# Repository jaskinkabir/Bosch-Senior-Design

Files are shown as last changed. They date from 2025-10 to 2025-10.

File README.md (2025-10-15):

# Intro
For my senior design project, my team was tasked with building an automated wash station for Bosch's grinder carts that are used to transport circular saw blades through the manufacturing process. My part of the project was designing and building the PLC system that controls the pressure washer, compressed air valves, and the wastewater pump. 

The project overview and final mechanical design can be seen in this poster
poster

# Initial Design
I began the design process by mapping out the Process Flow Diagram for the overall system, focusing on efficiency and robustness. My PLC system needed to control power to the pressure washer, the wastewater disposal pump, and the solenoid valves that control the flow of clean water, wastewater, and compressed air for drying.
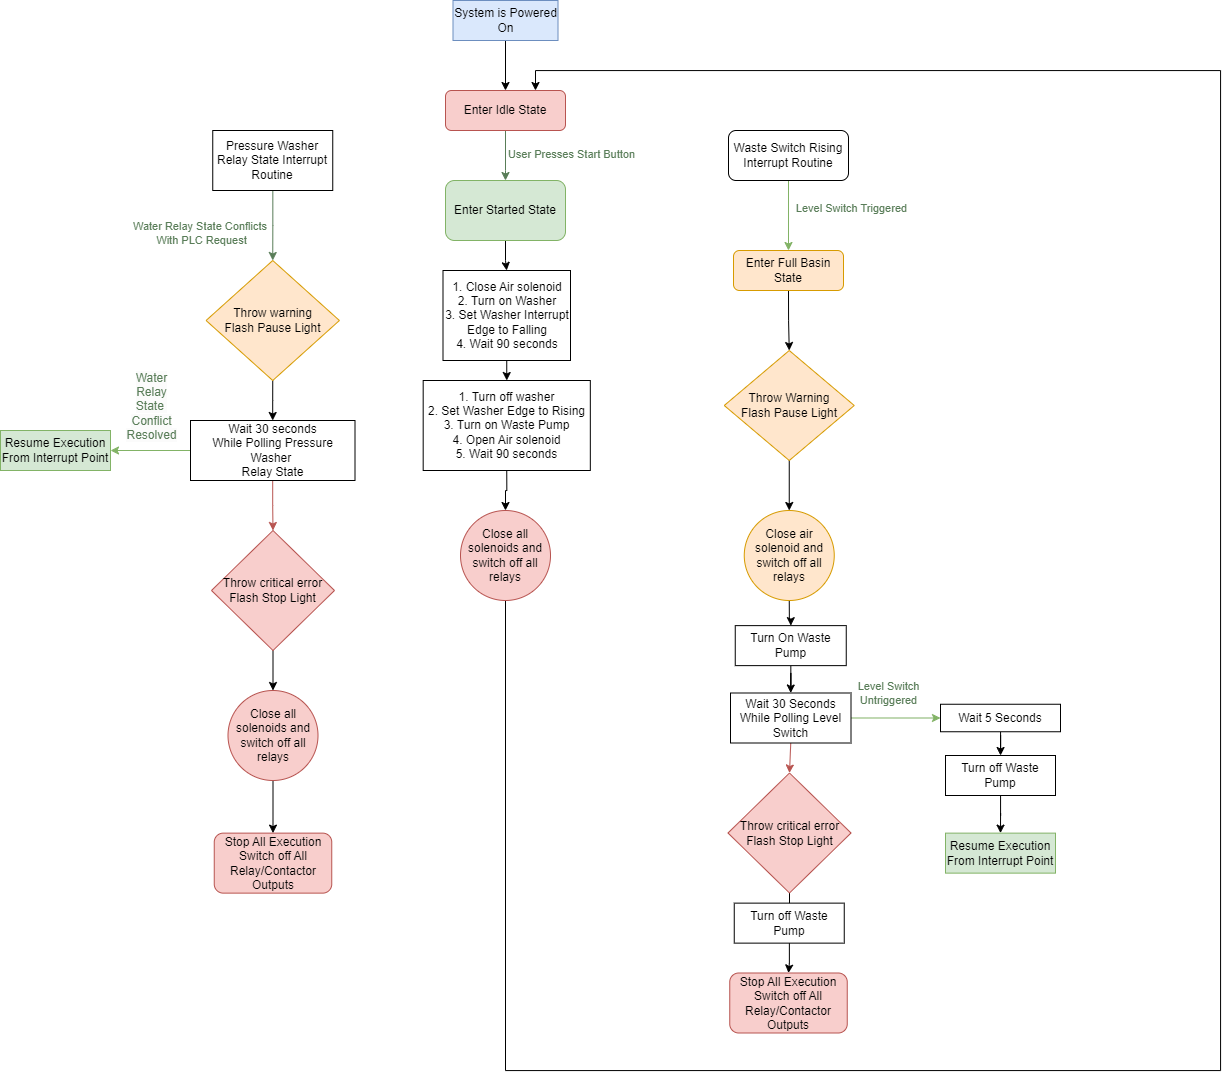
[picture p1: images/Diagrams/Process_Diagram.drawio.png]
PFD


## Relay Interlocking System
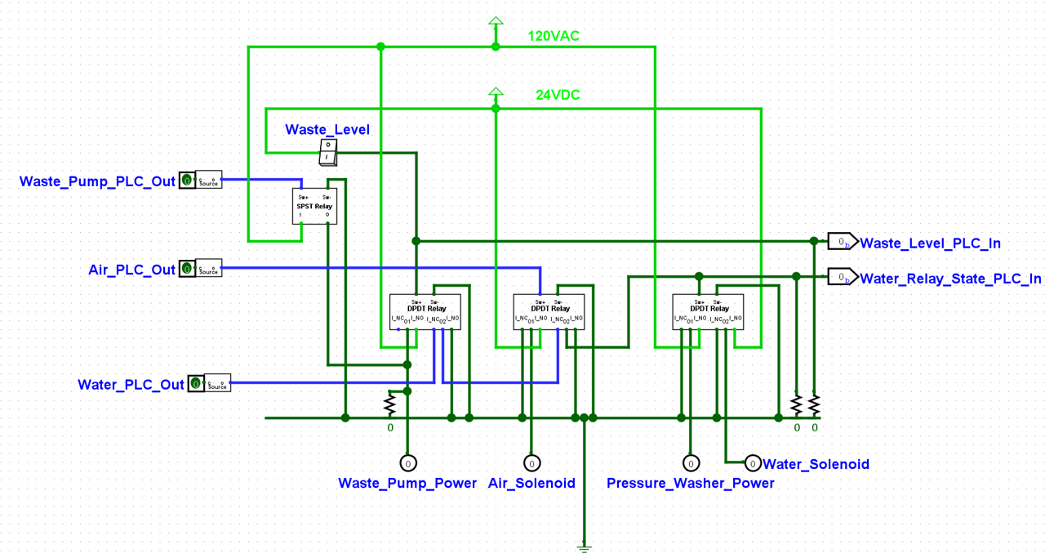
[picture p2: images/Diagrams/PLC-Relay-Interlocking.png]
relay_interlocking

I then designed a relay-interlocking system that ensures, in hardware, the following restrictions
- The pressure washer cannot be powered on, nor the water input solenoid be open while the compressed air solenoid is open
	- This is to ensure water does not enter Bosch's compressed air system
- The pressure washer cannot be powered, nor the water input solenoid be open while the wastewater level float switch is triggered. The wastewater level float switch also powers on the waste pump independently of the PLC
	- This is to ensure the system does not flood with wastewater
# PLC Design
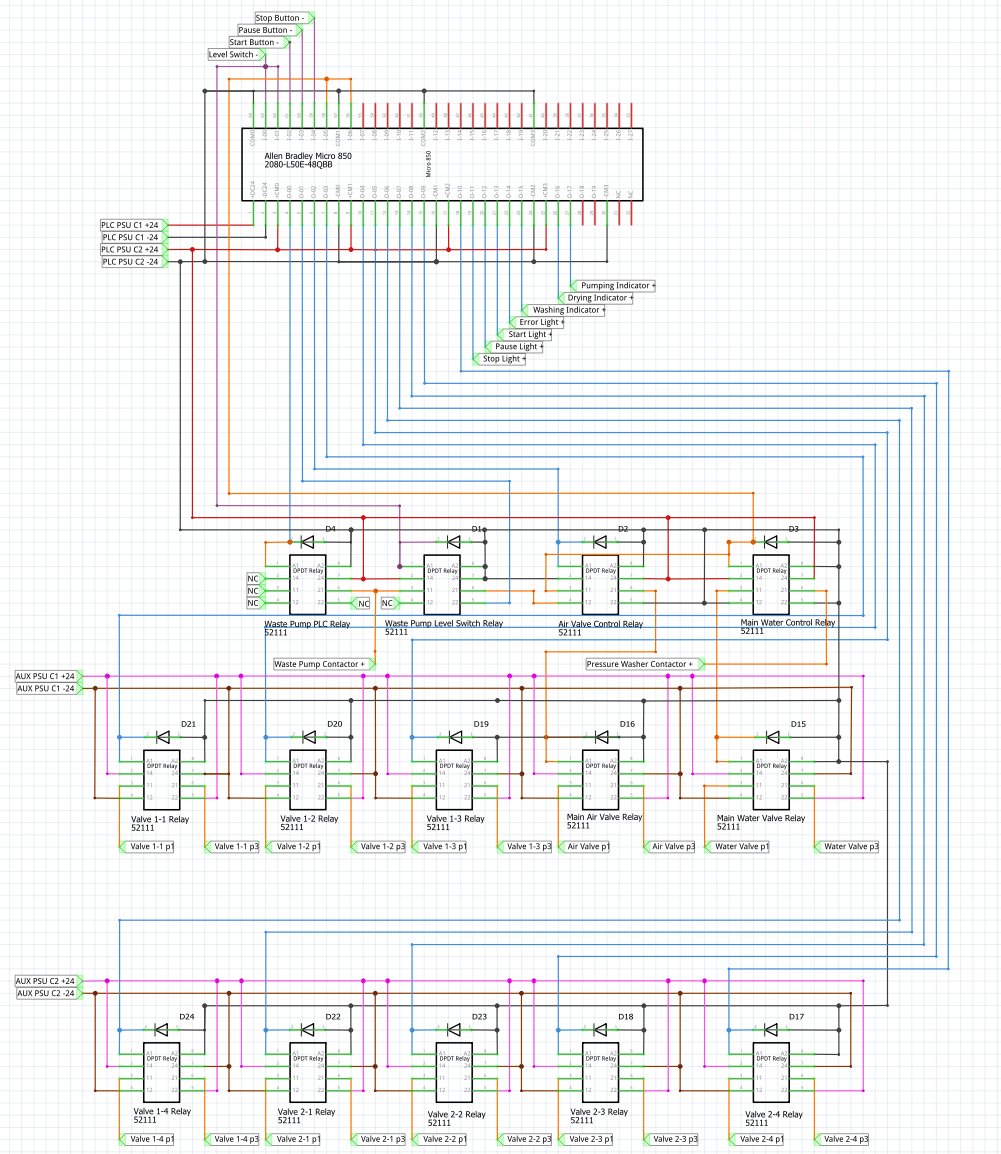
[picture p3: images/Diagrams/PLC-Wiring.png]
PLC_wiring

- Once the PLC was chosen, I created a wiring diagram for the PLC, the relays, and the relay protectors
- This diagram was extremely useful when I eventually assembled the system
## Python Netlist Analyzer
- Once I created the Fritzing diagram, I exported the netlist as an XML file
- I then wrote a Python script to analyze this netlist and convert it into a CSV file that contains each net, the number of nodes, and whether or not the net includes a node external to the PLC enclosure
- I used this CSV file for these purposes:
	- To gauge how much wire I needed to buy and of what color (since I assigned each net type a different color)
	- To figure out how many pins the external connectors needed
	- To make checking my final wiring against the initial design much easier
# Plywood Wiring
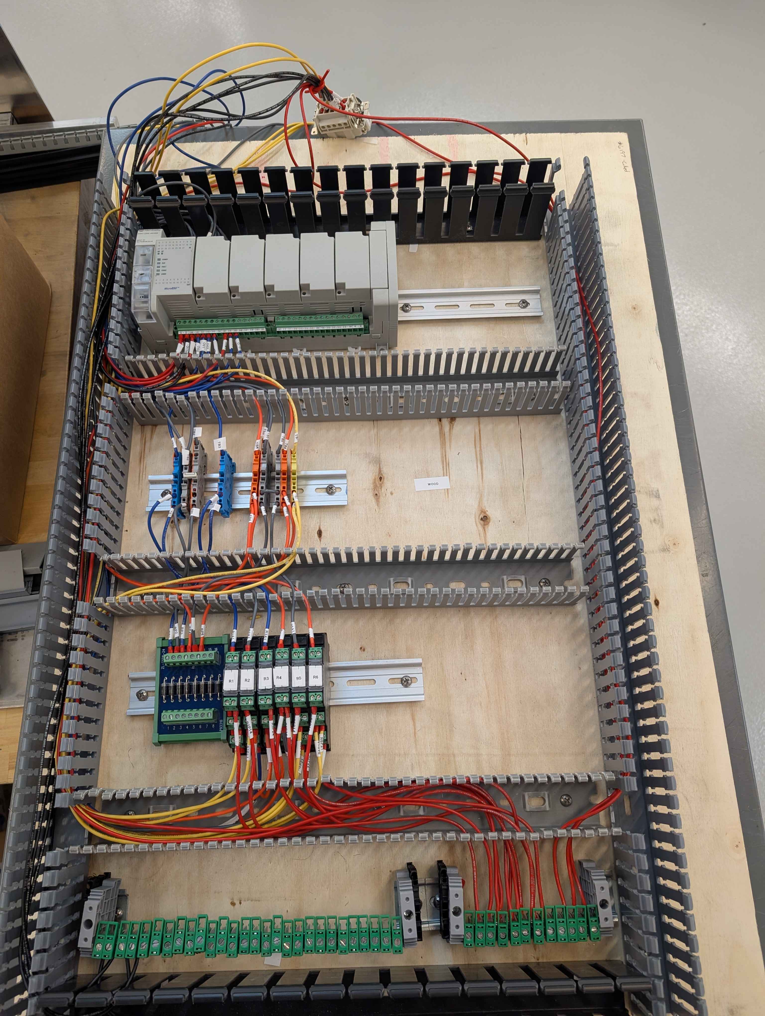
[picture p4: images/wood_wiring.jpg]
wood_wiring

- Due to ordering issues, the PLC enclosure did not arrive alongside the PLC and all its related components. 
- So as to not waste any time, I mounted all the components to a piece of plywood I bought from Home Depot and started cutting, labeling, and routing the wires according to the diagram and the CSV file
# Final Wiring
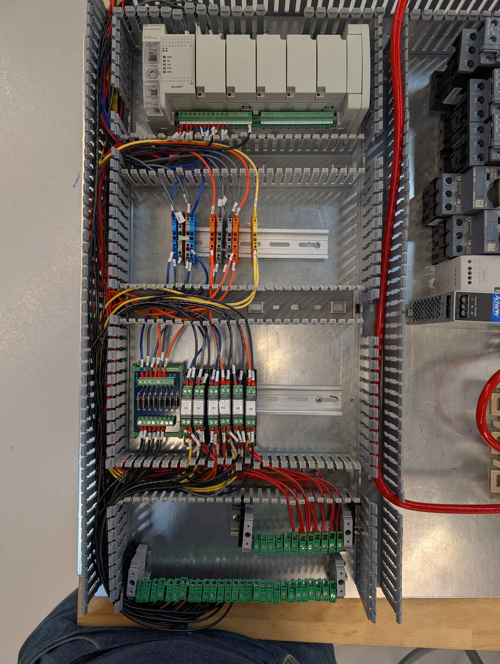
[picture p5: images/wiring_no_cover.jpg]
wiring_no_cover

final_wiring
- Once the enclosure for the PLC system arrived, I transferred over the components and wires from the plywood into the new enclosure
- I am very proud of the organization and cleanliness of the assembled system

# HMI Design
- For the control interface, I used a touchscreen HMI panel for displaying the system's state, and 3 physical buttons for controlling the machine
- I began with a wiring diagram:
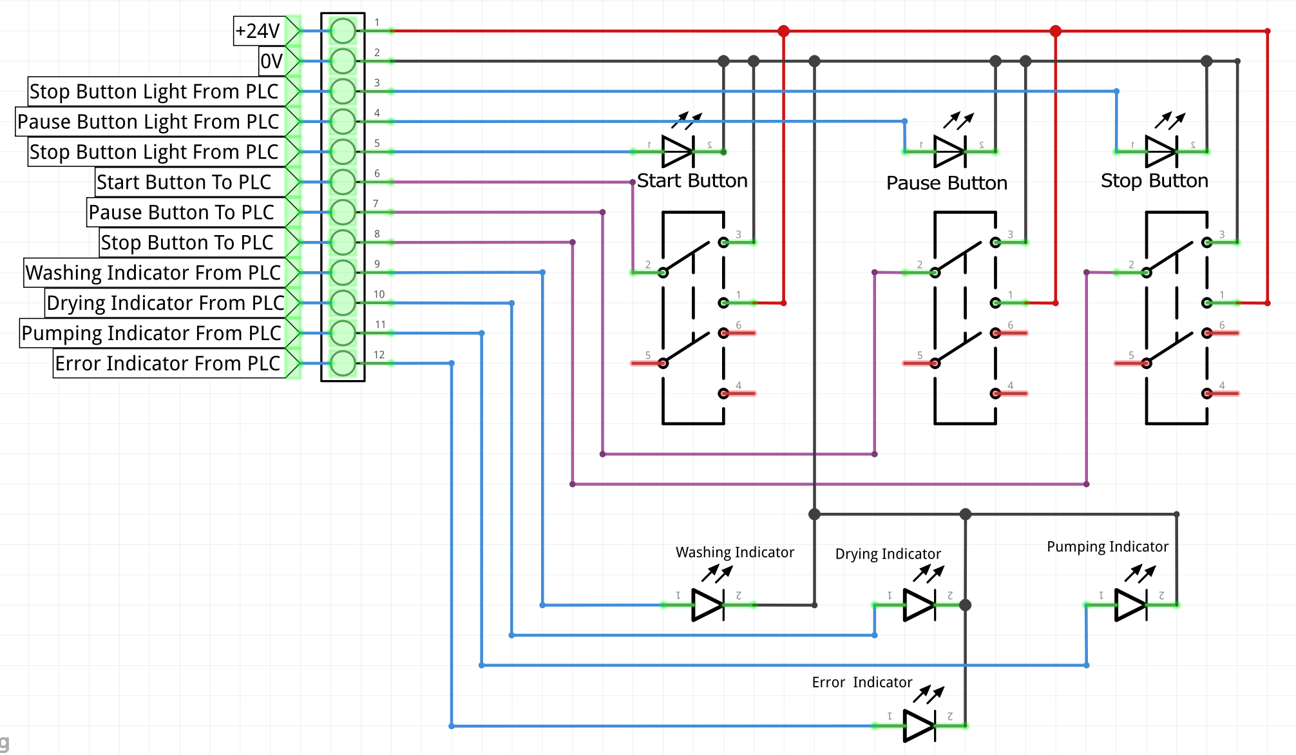
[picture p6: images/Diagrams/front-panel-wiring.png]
fp_wiring

- I then wired together the HMI enclosure and ran a waterproof cable to connect it to the PLC
# Conclusion
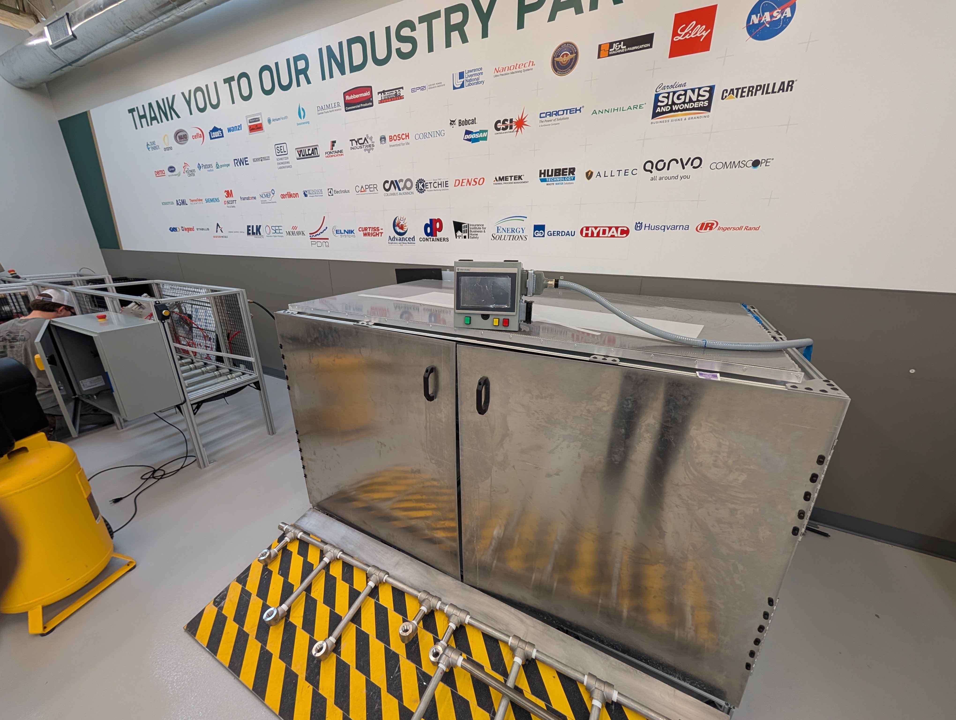
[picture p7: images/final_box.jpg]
final_box

Regrettably, due to timing constraints and ordering mishaps, I did not have the time to program the PLC. However, I still gained valuable experience from this project.

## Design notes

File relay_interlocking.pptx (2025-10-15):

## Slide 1

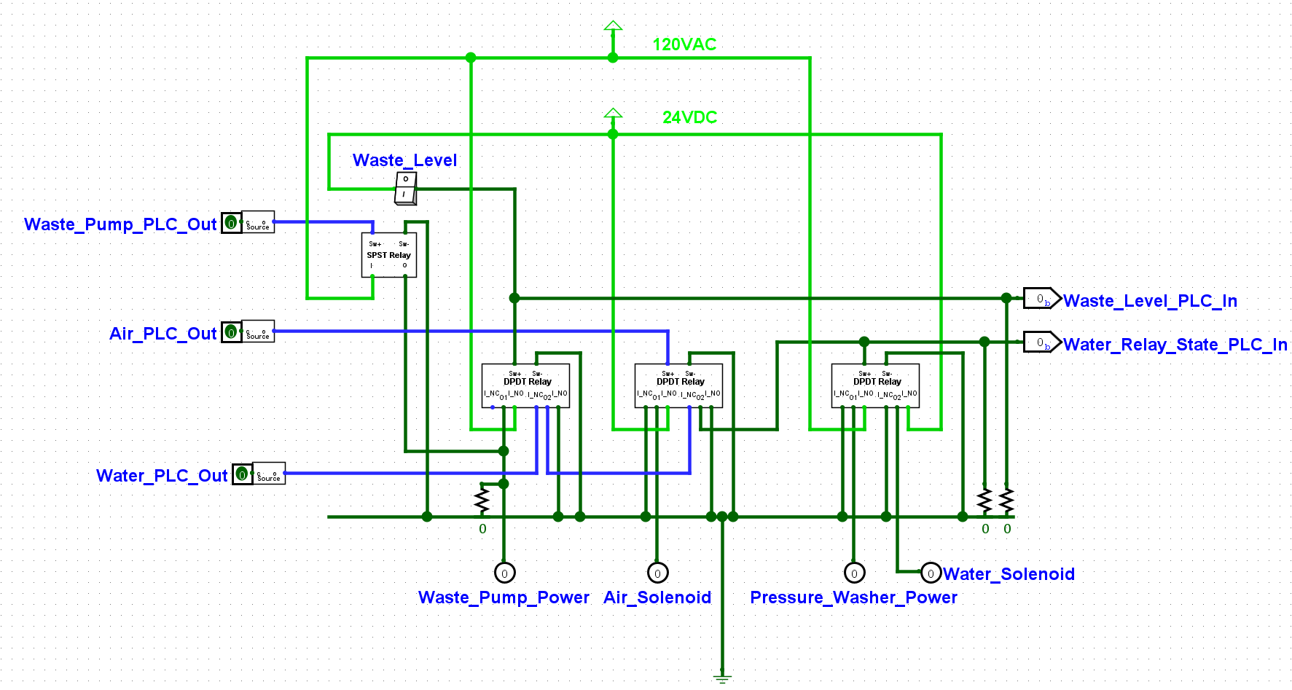
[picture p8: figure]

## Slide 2

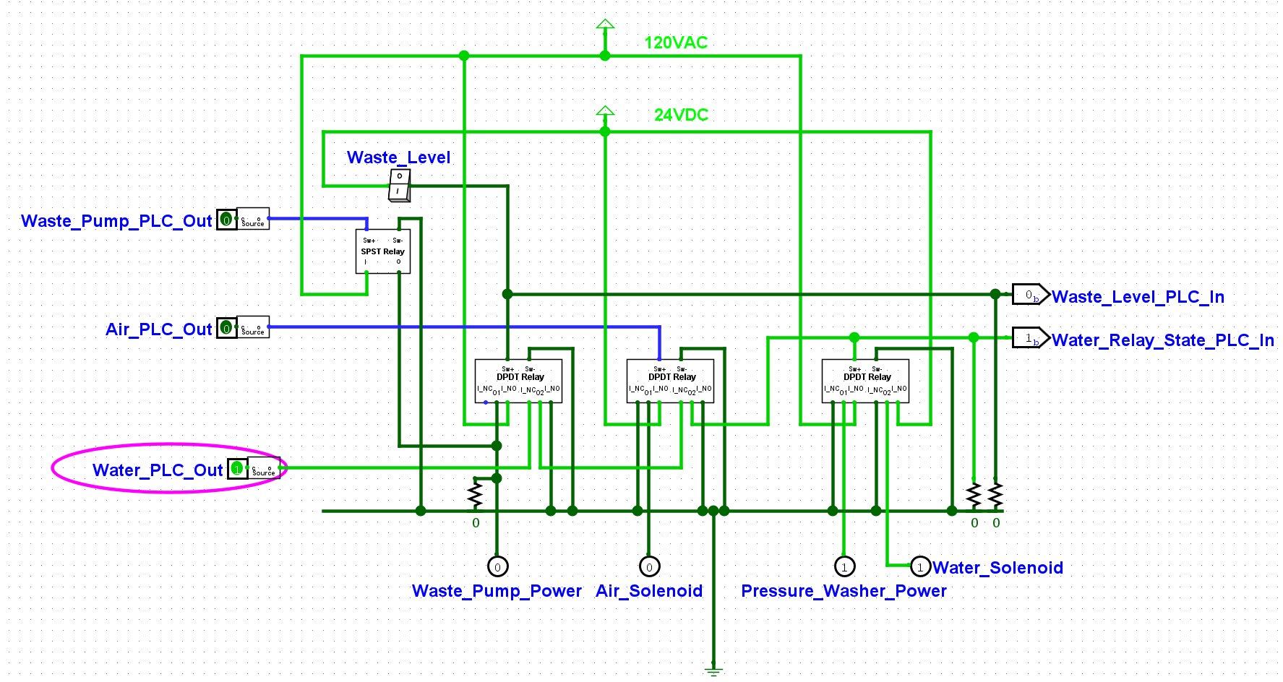
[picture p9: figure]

PLC Turns Water On

Main Water Solenoid
Receives 24VDC

Pressure washer receives 120VAC

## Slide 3

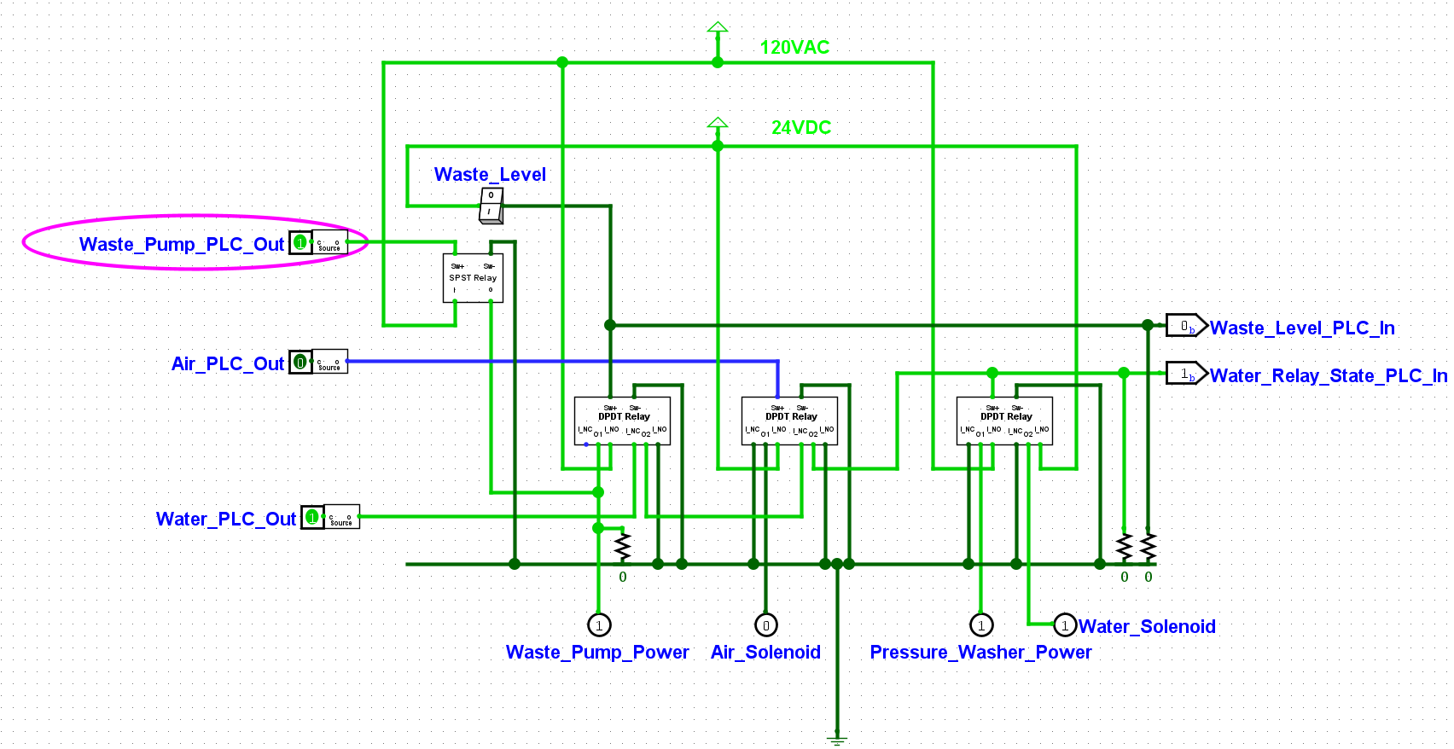
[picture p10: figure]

Waste pump enabled with short delay

Waste pump receives 120VAC

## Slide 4

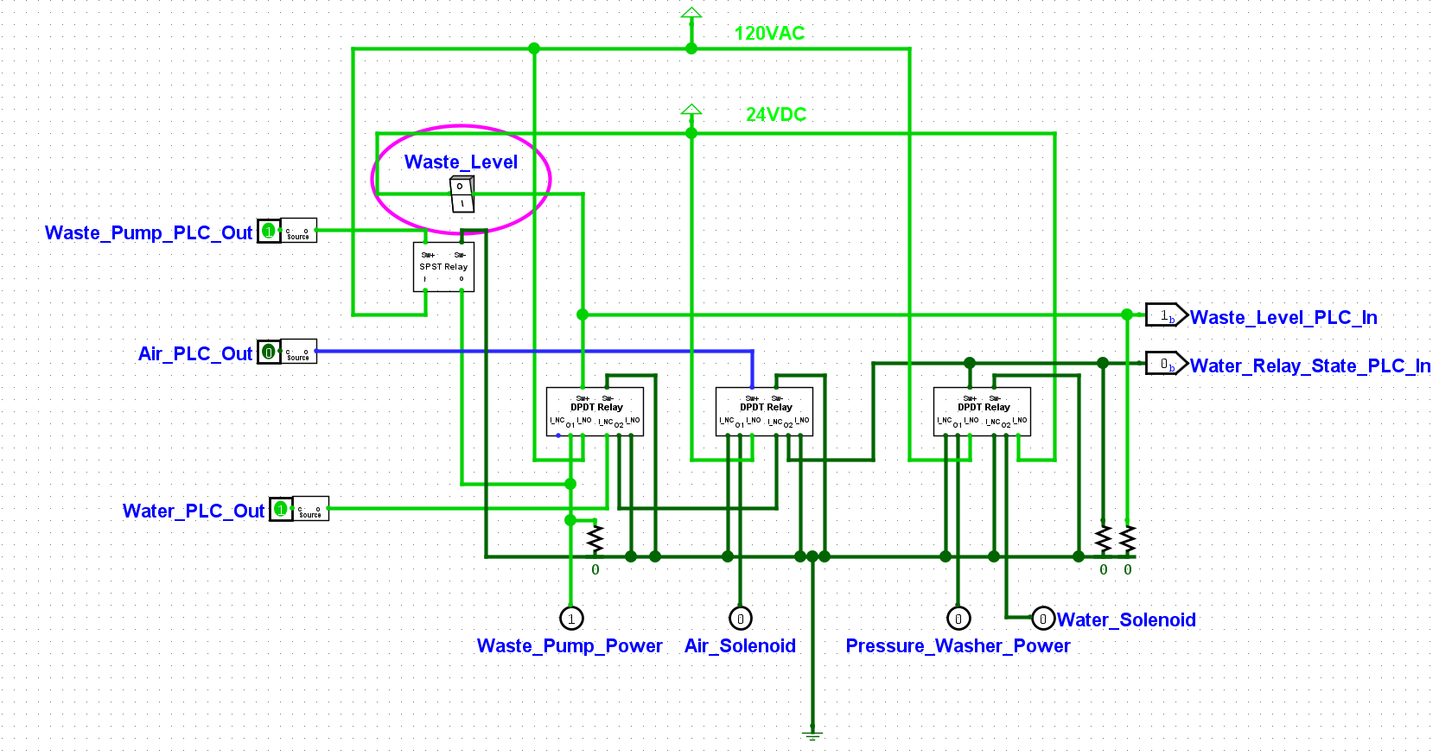
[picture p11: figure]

Waste level switch triggered

PLC can read switch state

Pressure Washer instantly turns off
and the solenoid is closed

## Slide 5

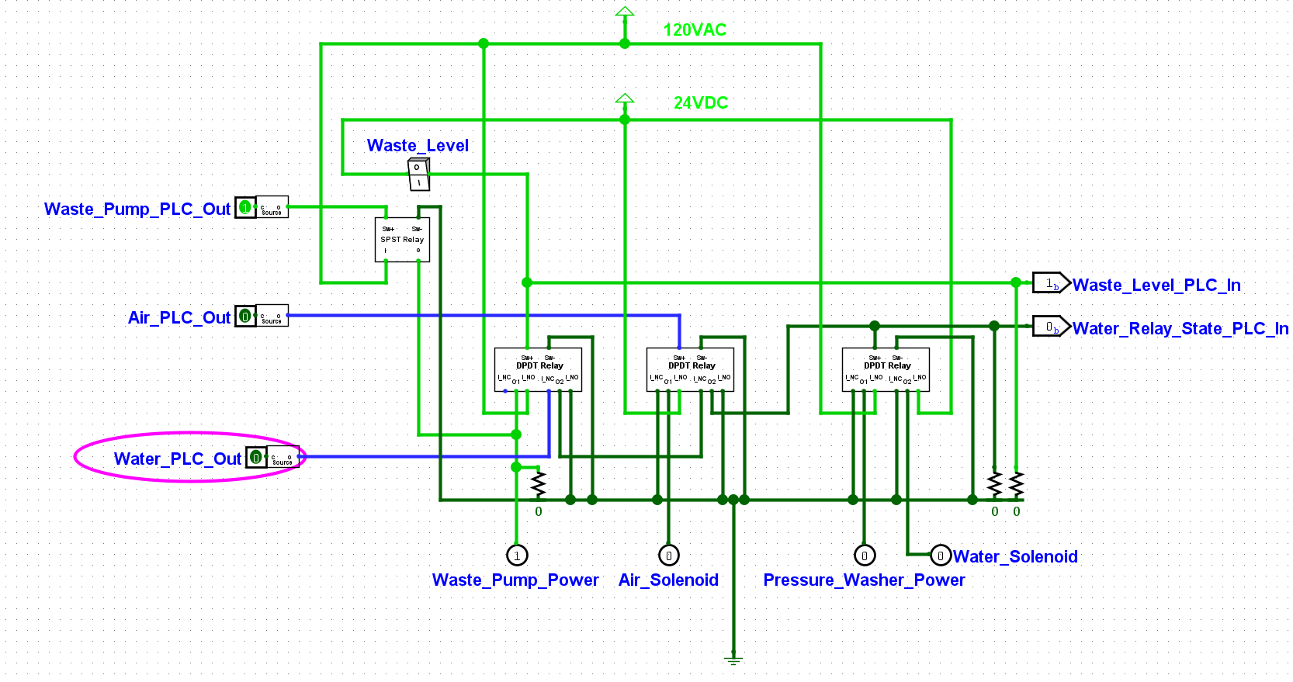
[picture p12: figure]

PLC holds pump on for set time

If level switch is still triggered after this time, throw critical error

PLC Switches its water output off
And pauses wash cycle

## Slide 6

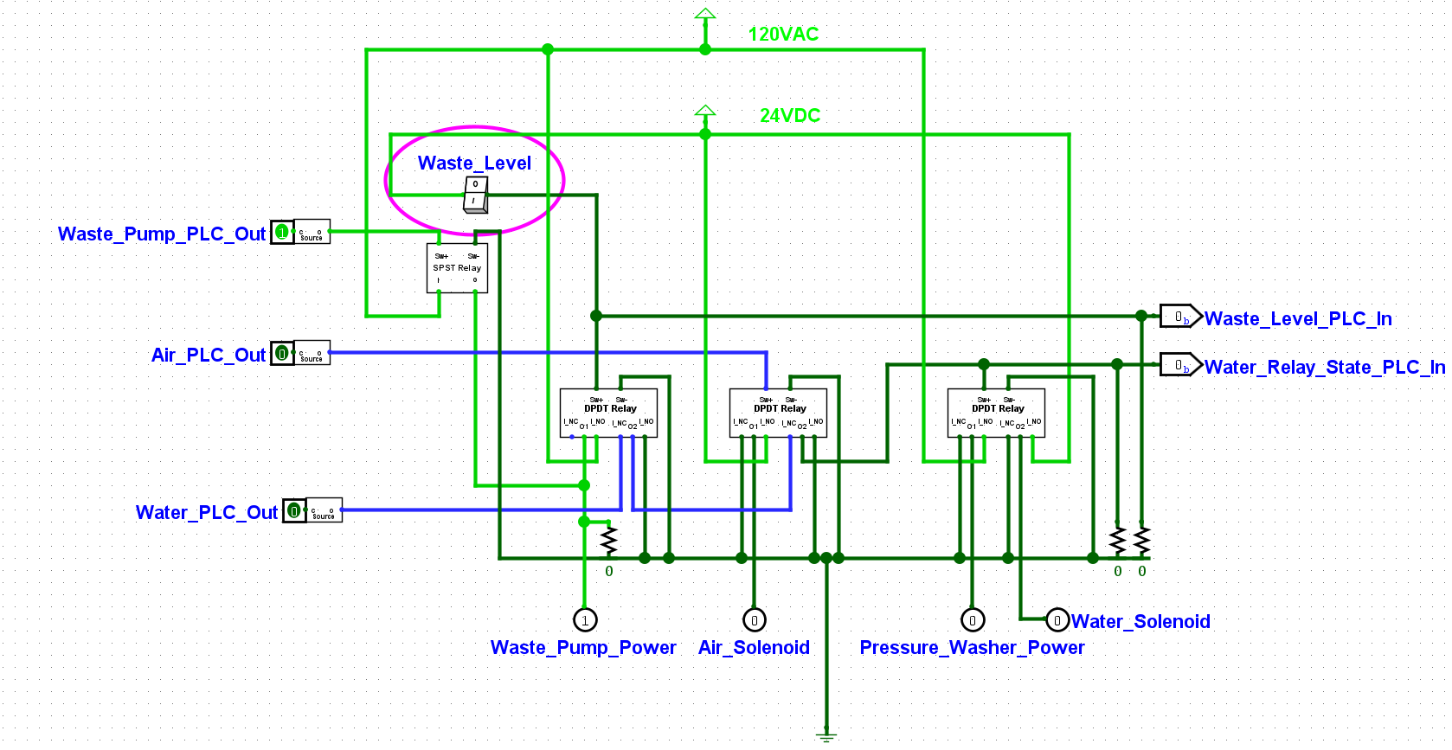
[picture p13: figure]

Level switch returns to normal position

PLC recognizes change in switch state

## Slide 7

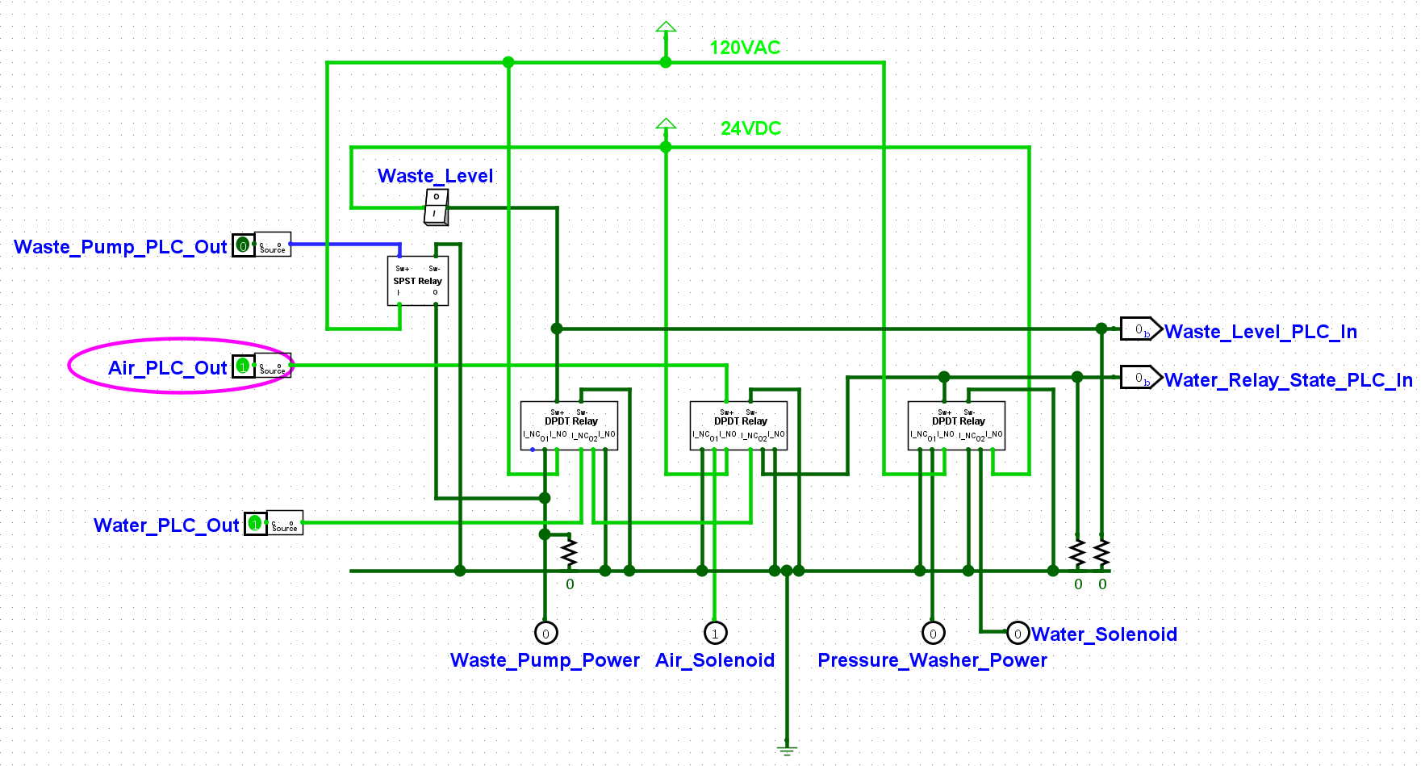
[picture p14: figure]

PLC disables waste pump in response to error

Software bug/PLC or Relay failure
opens air solenoid

PLC can recognize this error

Pressure washer turned off
Water solenoid closed

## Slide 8

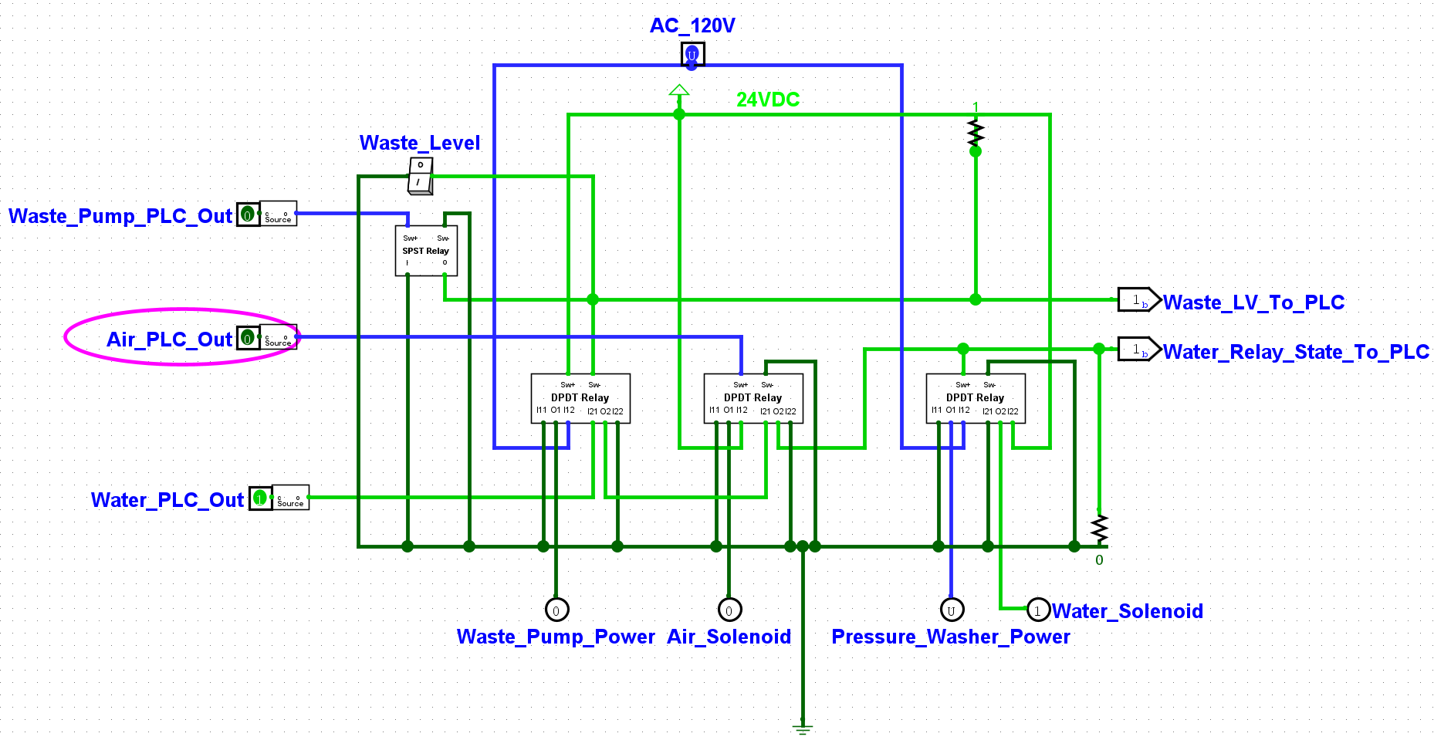
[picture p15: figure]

Bug is resolved

Resume Wash Cycle

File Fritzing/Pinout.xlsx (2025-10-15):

PIN | FUNCTION
I0 | Level Switch
I1 | Start Button
I2 | Pause Button
I3 | Stop Button
I4 | Water Solenoid State
PIN | FUNCTION
O0 | Waste Pump Relay
O1 | Pressure Washer Relay
O2 | Air Solenoid Relay
O3 | Solenoid 1-1
O4 | Solenoid 1-2
O5 | Solenoid 1-3
O6 | Solenoid 1-4
O7 | Solenoid 2-1
O8 | Solenoid 2-2
O9 | Solenoid 2-3
O10 | Solenoid 2-4
O11 | Stop Light
O12 | Pause Light
O13 | Start Light
O14 | Error Light
O15 | Washing Indicator
O16 | Drying Indicator
O17 | Pumping Indicator

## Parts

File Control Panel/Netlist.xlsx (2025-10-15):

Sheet: PLC_Diag_distributed_netlist
 | Net Name | # Nodes | External? | Type |  | Bus Rod Length | Bus bar length |  |  |  |  |  |  | 40
0 | AUX PSU C1 -24 | 64 | TRUE | AUX PSU C2 -24 | 213.3333333 | 48 | 49.9 | 19.64566929 |  |  | Net Counts |  | Wire color | Wire length | Spool length
1 | AUX PSU C2 +24 | 34 | TRUE | AUX PSU C2 +24 | 113.3333333 | 25.5 | 27.4 | 10.78740157 |  |  | AUX PSU C2 -24 | 64 | Black | 213.3333333 | 500 | 77.93 | #N/A
2 | PLC I-05 | 5 | FALSE | PLC Input |  |  |  |  |  |  | AUX PSU C2 +24 | 34 | Red | 113.3333333 | 200 | 37.4
3 | Level Switch - | 5 | TRUE | PLC Input |  |  |  |  |  |  | Logical Output | 45 | Yellow | 150 | 500 | 77.93
4 | MAV RL PA1 | 3 | FALSE | Interconnection |  |  |  |  |  |  | PLC Output | 46 | Blue | 153.3333333 | 200 | 37.4
5 | MWV RL PA1 | 3 | FALSE | Interconnection |  | 73.5 | 77.3 | Cm |  |  | PLC Input | 16 | Grey | 53.33333333 | 100 | 20.78
6 | Waste Pump Contactor + | 3 | TRUE | Logical Output |  | 28.93700787 | 30.43307087 | In |  |  | Interconnection | 8 | Orange | 26.66666667 | 25 | 6.3
7 | PLC O-00 | 3 | FALSE | PLC Output
8 | PLC O-02 | 3 | FALSE | PLC Output |  | Bus Terminals |  |  |  |  |  |  |  | 710 | 1525 | 257.74
9 | PLC O-03 | 3 | FALSE | PLC Output |  | 98 | 490 |  |  |  |  |  |  | 2.366666667 | 5.083333333
10 | PLC O-04 | 3 | FALSE | PLC Output
11 | PLC O-05 | 3 | FALSE | PLC Output |  |  | 2 port terminal blocks | 3 Port TB | 4 Port TB |  |  |  |  |  |  | 178.03
12 | PLC O-06 | 3 | FALSE | PLC Output |  | Single Circuit | 33 | 13 | 2 |  |  | 25 | 6.3
13 | PLC O-07 | 3 | FALSE | PLC Output |  | Jumped |  | 2 |  |  |  | 50 | 11.43
14 | PLC O-08 | 3 | FALSE | PLC Output |  |  |  |  |  |  |  | 100 | 20.78
15 | PLC O-09 | 3 | FALSE | PLC Output |  | Total | 33 | 15 | 2 |  |  | 200 | 37.4
16 | PLC O-10 | 3 | FALSE | PLC Output |  |  |  |  |  |  |  | 500 | 77.93
17 | MAV PLC RL P12 | 2 | FALSE | Interconnection
18 | Air Valve p1 | 2 | TRUE | Logical Output |  | 0
19 | Air Valve p3 | 2 | TRUE | Logical Output
20 | Pressure Washer Contactor + | 2 | TRUE | Logical Output |  | Meaning | Color | 2 Port | 3 port | 4 Port
21 | Valve 1-1 p1 | 2 | TRUE | Logical Output
22 | Valve 1-1 p3 | 2 | TRUE | Logical Output |  | Logical Output | Yellow | 21 | 1
23 | Valve 1-2 p1 | 2 | TRUE | Logical Output |  | PLC Output | Blue | 7 | 10
24 | Valve 1-2 p3 | 2 | TRUE | Logical Output |  | PLC Input | Grey | 3 | 2 | 2
25 | Valve 1-3 p1 | 2 | TRUE | Logical Output |  | Interconnection | Orange | 1 | 2
26 | Valve 1-3 p3 | 2 | TRUE | Logical Output
27 | Valve 1-4 p1 | 2 | TRUE | Logical Output |  | 500
28 | Valve 1-4 p3 | 2 | TRUE | Logical Output |  |  |  | 32 | 15 | 2
29 | Valve 2-1 p1 | 2 | TRUE | Logical Output
30 | Valve 2-1 p3 | 2 | TRUE | Logical Output
31 | Valve 2-2 p1 | 2 | TRUE | Logical Output
32 | Valve 2-2 p3 | 2 | TRUE | Logical Output |  | Meaning | Color | 2 Port | 3 port | 4 Port |  | Total | Length of Blocks
33 | Valve 2-3 p1 | 2 | TRUE | Logical Output
34 | Valve 2-3 p3 | 2 | TRUE | Logical Output |  | Logical Output | Yellow | 21 | 1 |  |  | 22 | 9.24
35 | Valve 2-4 p1 | 2 | TRUE | Logical Output |  | PLC Output | Blue | 8 | 10 |  |  | 18 | 7.56
36 | Valve 2-4 p3 | 2 | TRUE | Logical Output |  | Interconnection | Orange | 1 | 2 |  |  | 3 | 1.26
37 | Water Valve p1 | 2 | TRUE | Logical Output |  | PLC Input | Grey | 3 | 2 | 2 |  | 7 | 2.94
38 | Water Valve p3 | 2 | TRUE | Logical Output
39 | PLC PSU C1 +24 | 2 | TRUE | PLC PSU C1 +24 |  |  |  |  |  |  |  |  | 21
40 | PLC PSU C1 -24 | 2 | TRUE | PLC PSU C1 -24
41 | Pause Button - | 2 | TRUE | PLC Input |  |  |  | 33 | 15 | 2
42 | Start Button - | 2 | TRUE | PLC Input
43 | Stop Button - | 2 | TRUE | PLC Input
44 | PLC O-01 | 2 | FALSE | PLC Output
45 | Drying Indicator + | 2 | TRUE | PLC Output
46 | Error Light + | 2 | TRUE | PLC Output
47 | Pause Light + | 2 | TRUE | PLC Output
48 | Pumping Indicator + | 2 | TRUE | PLC Output
49 | Start Light + | 2 | TRUE | PLC Output
50 | Stop Light + | 2 | TRUE | PLC Output | 30
51 | Washing Indicator + | 2 | TRUE | PLC Output

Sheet: BOM
Part | Part # | Cost | Qty | Total Cost | Link
Bus Bar Terminal Block | 1529T11 | 1.022 | 100 | 102.2 |  | Total Cost
Bus Bar Mount | 1529T32 | 2.066 | 5 | 10.33 |  | 1061.78
Bus Bar Rod | 1529T21 | 31.42 | 1 | 31.42
Yellow 2 port Terminal Block | 9473T173 | 1.95 | 21 | 40.95 | https://www.mcmaster.com/9473T173/
Blue 2 port Terminal Block | 9473T173 | 1.95 | 8 | 15.6 | https://www.mcmaster.com/9473T173/
Orange 2 Port Terminal Block | 9473T173 | 1.95 | 1 | 1.95 | https://www.mcmaster.com/9473T173/
Grey 2 Port Terminal Block | 9473T173 | 1.95 | 3 | 5.85 | https://www.mcmaster.com/9473T173/
Yellow 3 port Terminal Block | 9473T177 | 2.58 | 1 | 2.58 | https://www.mcmaster.com/9473T177/
Blue 3 port Terminal Block | 9473T177 | 2.58 | 10 | 25.8 | https://www.mcmaster.com/9473T177/
Orange 3 Port Terminal Block | 9473T177 | 2.58 | 2 | 5.16 | https://www.mcmaster.com/9473T177/
Grey 3 Port Terminal Block | 9473T177 | 2.58 | 2 | 5.16 | https://www.mcmaster.com/9473T177/
Grey 4 Port Terminal Block | 9473T182 | 2.97 | 2 | 5.94 | https://www.mcmaster.com/9473T182/
Jumper | 9473T194 | 1.51 | 2 | 3.02 | https://www.mcmaster.com/9473T194/
16 Pin Connector Male | ZP-MC16B-1-MC016-2 | 8 | 6 | 48 | https://www.automationdirect.com/adc/shopping/catalog/wiring_solutions/multi-wire_connectors/inserts/zp-mc16b-1-mc016-2 |  |  | Worked from 3-8:55 9/4
16 Pin Connector Female | ZP-MC16B-1-FC016-2 | 7.25 | 3 | 21.75 | https://www.automationdirect.com/adc/shopping/catalog/wiring_solutions/multi-wire_connectors/inserts/zp-mc16b-1-fc016-2
16 Pin Connector Hood | ZP-MC16B-2-STE21M | 14.5 | 3 | 43.5 | https://www.automationdirect.com/adc/shopping/catalog/wiring_solutions/multi-wire_connectors/housings/zp-mc16b-2-ste21m
16 Pin Connector Base | ZP-MC16B-2-SBHC | 25 | 3 | 75 | https://www.automationdirect.com/adc/shopping/catalog/wiring_solutions/multi-wire_connectors/housings/zp-mc16b-2-sbhc
Code Pins | ZP-MC-CODEPIN-2 | 10.5 | 1 | 10.5 | https://www.automationdirect.com/adc/shopping/catalog/wiring_solutions/multi-wire_connectors/code_pins_-z-_polarization_keys/zp-mc-codepin-2
Crimp Contacts Male | ZP-MC-CC-M16A-18 | 34.5 | 1 | 34.5 | https://www.automationdirect.com/adc/shopping/catalog/wiring_solutions/multi-wire_connectors/crimp_contacts/zp-mc-cc-m16a-18
Crimp Contacts Female | ZP-MC-CC-F16A-18 | 32 | 1 | 32 | https://www.automationdirect.com/adc/shopping/catalog/wiring_solutions/multi-wire_connectors/crimp_contacts/zp-mc-cc-f16a-18
PLC Enclosure | SCE-36N2408LP | 320 | 1 | 320 | https://www.automationdirect.com/adc/shopping/catalog/enclosures_-a-_racks/wall-mount_enclosures/sce-36n2408lp
PLC Enclosure Sub Panel | SCE-36N24MPP | 129 | 1 | 129 | https://www.automationdirect.com/adc/shopping/catalog/enclosures_-a-_racks/subpanels/sce-36n24mpp
HMI/Button Enclosure | SCE-8N804LP | 55 | 1 | 55 | https://www.automationdirect.com/adc/shopping/catalog/enclosures_-a-_racks/wall-mount_enclosures/sce-8n804lp
HMI/Button Sub Panel | SCE-8N8MPP | 14.75 | 1 | 14.75 | https://www.automationdirect.com/adc/shopping/catalog/enclosures_-a-_racks/subpanels/sce-8n8mpp
Wire Ferrules | 7950K71 (https://www.mcmaster.com/7950K71) | 10.91 | 2 | 21.82 | https://www.mcmaster.com/7950K71/ | 25 | 6.3
Black wire 500ft |  |  |  |  | https://www.mcmaster.com/8054T15/ | 50 | 11.43
Red Wire 200ft |  |  |  |  | https://www.mcmaster.com/8054T15/ | 100 | 20.78
Yellow Wire 500ft |  |  |  |  | https://www.mcmaster.com/8054T15/ | 200 | 37.4
Grey Wire 200ft |  |  |  |  | https://www.mcmaster.com/8054T15/ | 500 | 77.93
Orange Wire 25ft |  |  |  |  | https://www.mcmaster.com/8054T15/

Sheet: Connectors
Destination | Pin list | Pin Count | Destination | Pin list | Pin Count |  | Destination | Pin list | Pin Count | Destination | Pin list | Pin Count
Electrical Box | PLC PSU + | 10 | Valves | Valve 1-1 p1 | 16 |  | Button Panel | Start Button - | 12 | Basin | Level Switch + | 2
 | PLC PSU - |  |  | Valve 1-1 p3 |  |  |  | Pause Button - |  |  | Level Switch -
 | AUX PSU C1+ |  |  | Valve 1-2 p1 |  |  |  | Stop Button -
 | AUX PSU C1- |  |  | Valve 1-2 p3 |  |  |  | Start Light +
 | AUX PSU C2+ |  |  | Valve 1-3 p1 |  |  |  | Pause Light +
 | AUX PSU C2- |  |  | Valve 1-3 p3 |  |  |  | Stop Light +
 | WP CT + |  |  | Valve 1-4 p1 |  |  |  | Washing Light +
 | WP CT - |  |  | Valve 1-4 p3 |  |  |  | Drying Light +
 | PW CT + |  |  | Valve 2-1 p1 |  |  |  | Pumping Light +
 | PW CT - |  |  | Valve 2-1 p3 |  |  |  | Error Light +
 |  |  |  | Valve 2-2 p1 |  |  |  | Button Panel +
 |  |  |  | Valve 2-2 p3 |  |  |  | Button Panel -
 |  |  |  | Valve 2-3 p1
 |  |  |  | Valve 2-3 p3
 |  |  |  | Valve 2-4 p1
 |  |  |  | Valve 2-4 p3
 |  |  |  |  |  | 76

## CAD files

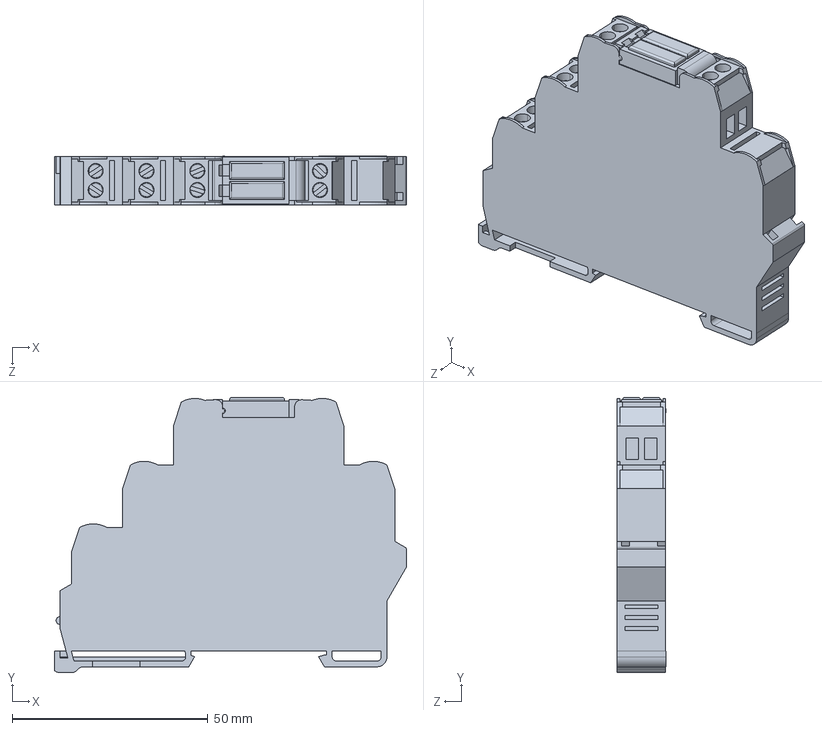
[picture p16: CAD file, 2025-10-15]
Control Panel/Models/Relay.STEP
90.0 x 70.4 x 12.5 mm

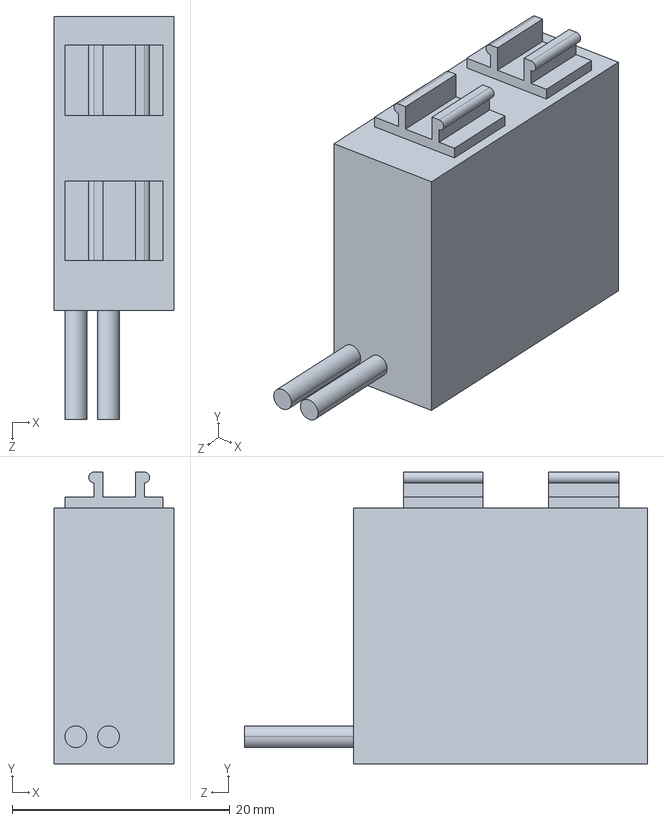
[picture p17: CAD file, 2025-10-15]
Control Panel/Models/Relay_Protector.STEP
11.0 x 26.8 x 37.0 mm

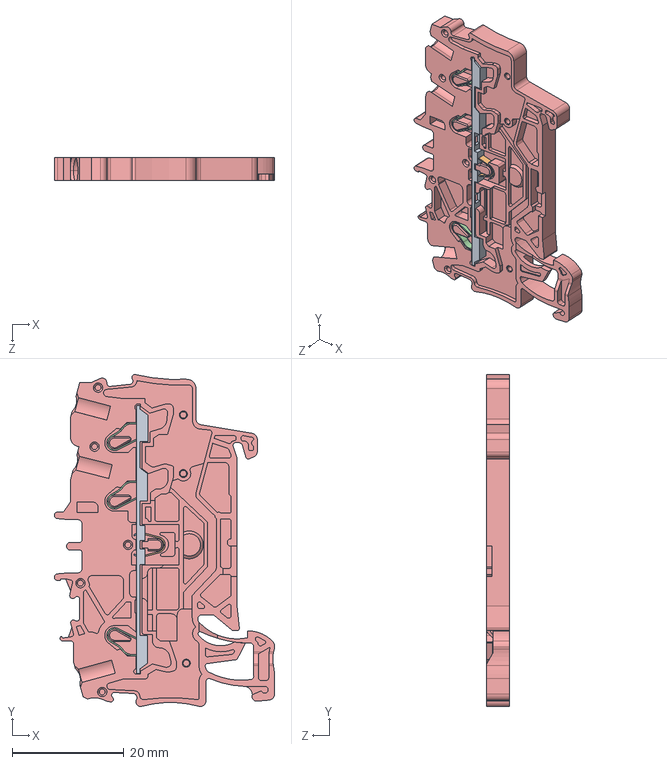
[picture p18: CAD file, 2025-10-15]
Control Panel/Models/9473T179_Quick and Secure Modular DIN-Rail Terminal Block.STEP
39.5 x 59.5 x 4.20 mm

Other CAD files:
Control Panel/Models/2080-L50E-48QBB.sldasm
Control Panel/Models/2080-L50E-48QBB_base.sldprt
Control Panel/Models/2080-L50E-48QBB_side_cover.sldprt
Control Panel/Models/2080-L50E-48QBB_top_cover.sldprt
Control Panel/Models/2080-L50E-48QBB.SLDPRT

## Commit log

2025-10-15 added project summary to README
    [2080-L50E-48QBB.SLDPRT, 2080-L50E-48QBB.sldasm, 2080-L50E-48QBB_base.sldprt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]
2025-10-15 renamed powerpoint
